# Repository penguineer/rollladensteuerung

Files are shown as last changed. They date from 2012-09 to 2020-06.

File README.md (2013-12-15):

Rolladensteuerung
=================

Content

controller:       Relais-Controller Rollläden
manuellsteuerung: Schalter für Manuellbetrieb Rollläden
raspberry:        Software für den Kontroll-Raspy
relaiskarte:      Relais Rollläden
switchboard:      Altes Schalterboard
tuer-controller:  I2C-Bridge zur Tür-Steuerung
tuer-steuerung:   Kontrolle Motor und Türstatus-Schalter
wd-switch:        Watchdog-Switch für Reset per Raspy

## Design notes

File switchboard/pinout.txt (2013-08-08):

DSUB:
pin#	funcion (0/1)
1	vcc
2	out 1 (up/down)
3	out 2 (up/down)
4	out 3 (up/down)
5	out 4 (up/down)
6	out 1 (off/on)
7	out 2 (off/on)
8	out 3 (off/on)
9	out 4 (off/on)

Molex:
1	5V
2	GND
3	GND
4	12V - not used

orange headers:
2pin	230V in
3pin	GND-UP-DOWN

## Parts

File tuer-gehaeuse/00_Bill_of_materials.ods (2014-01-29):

Pos.Nr. | Titel | Material | Menge | Bemerkung | Bezugsquellen | PDF | DXF | STL
1 | Schließblech | Stahl | 1 | Bereits vorhanden | -o-
2 | Sechskantschraube ISO 4017 - M6x30 | Stahl | 2 |  | Ebay/Baumarkt
3 | Scheibe ANSI B18.22M regulär 6 mm | Stahl | 13 |  | Ebay/Baumarkt
4 | Sechskantmutter ISO 4032 - M6 | Stahl | 14 |  | Ebay/Baumarkt
5 | Tür-Motor-Koppler | Holz, Kiefer | 1 |  | Baumarkt | File | File | File
6 | Sechskantschraube ISO 4017 - M6x80 | Stahl | 4 |  | Ebay/Baumarkt
7 | Getriebemotor | Materialverbund | 1 |  | http://www.pollin.de/shop/dt/MjI1OTg2OTk-/Motoren/DC_Getriebemotoren/Gleichstrom_Getriebemotor_GMPD_404980_1_12_V_.html
8 | Drehring | ABS Plastik, hochfest | 1 | Bestandteil des Motors | -o-
9 | Schlüsselhalter | ABS Plastik, hochfest | 1 | Kopf ist an Schlüssel anzupassen | Internet | File |  | File
10 | Ritzel | Acryl | 1 |  | Ebay | File | File
11 | Zahnrad | Acryl | 1 |  | Ebay | File | File
12 | Kugellager 608Z Di=8mm Da=22m | Stahl | 2 |  | Ebay
13 | M8x80 Gewindestange | Stahl | 1 | Als Welle für Zahnrad | Ebay/Baumarkt
14 | M8 Mutter | Stahl | 5 |  | Ebay/Baumarkt
15 | Washer DIN 6902 - A M8 - 200 HV | Stahl | 2 |  | Ebay/Baumarkt
16 | Gehäuseverbinder | Holz, Kiefer | 1 |  | Baumarkt | File |  | File
17 | Gehäusehälfte 2 | Holz, Kiefer | 1 |  | Baumarkt | File | File | File
18 | Spacer: Motor-Ritzel | PLA | 1 |  | Internet | File | File | File
19 | Exzenter | PLA | 2 |  | Internet | File |  | File
20 | M3x12-Senkkopfschraube | Stahl | 2 | Zur Montage der Exzenter | Ebay/Baumarkt
21 | Endschalter | Materialverbund | 2 |  | http://reprapuniverse.com/catalog/product_info.php?cPath=28&products_id=41
22 | Drahtstift | Stahl | 4 | Nicht eingezeichnet, zur Montage der Endschalter | Ebay/Baumarkt
23 | Spacer: Enschalter-Hälfte 2 | Holz, Kiefer | 1 |  | Baumarkt | File | File | File
24 | Fassschutz_hinten | Acryl | 1 |  | Ebay | File | File
25 | Fassschutz_vorn | Acryl | 1 |  | Ebay | File | File
26 | Fassschutz_oben | Acryl | 1 |  | Ebay | File | File
27 | Fassschutz_rechts | Acryl | 1 |  | Ebay | File | File
28 | Fassschutz_links | Acryl | 1 |  | Ebay | File | File
29 | Fassschutz_unten | Acryl | 1 |  | Ebay | File | File
30 | 3mm LED rot | Materialverbund | 3 | Nicht eingezeichnet, werden in Fassschutz_hinten geklebt | http://www.ebay.de/itm/370921378597?ssPageName=STRK:MEWNX:IT&_trksid=p3984.m1439.l2649
31 | 3mm LED grün | Materialverbund | 3 | Nicht eingezeichnet, werden in Fassschutz_vorn geklebt | http://www.ebay.de/itm/370921405223?ssPageName=STRK:MEWNX:IT&_trksid=p3984.m1439.l2649

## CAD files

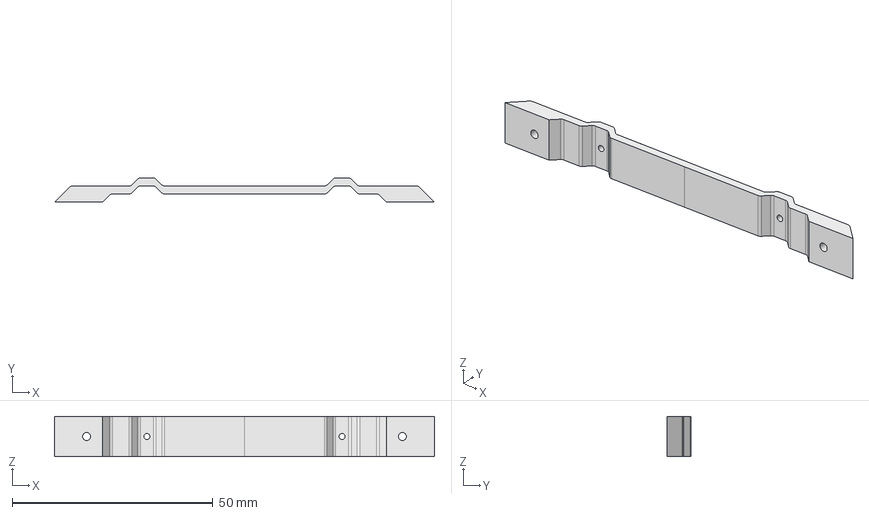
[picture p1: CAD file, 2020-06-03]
pi-hat/halterung.FCStd
94.6 x 6.00 x 10.0 mm

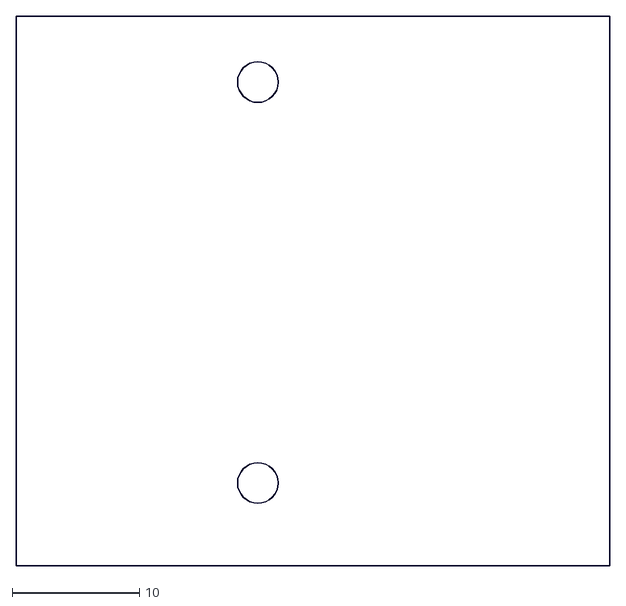
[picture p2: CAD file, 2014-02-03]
tuer-controller/tuer-controller-dim.dxf
46.7 x 43.2

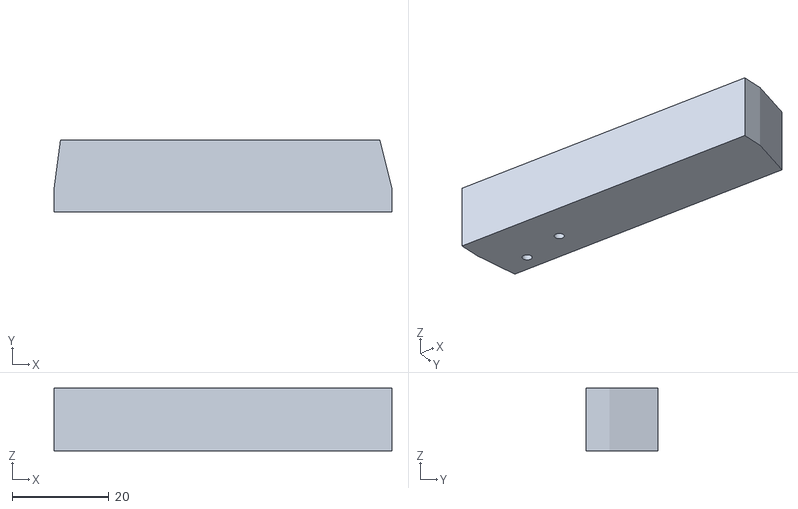
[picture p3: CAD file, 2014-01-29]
tuer-gehaeuse/Endschalter-Haelfte2.stl
70.0 x 15.0 x 13.0

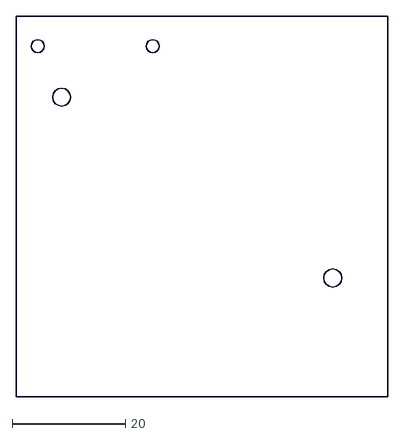
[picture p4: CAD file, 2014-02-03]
tuer-steuerung/tuer-steuerung-dim.dxf
65.7 x 67.3

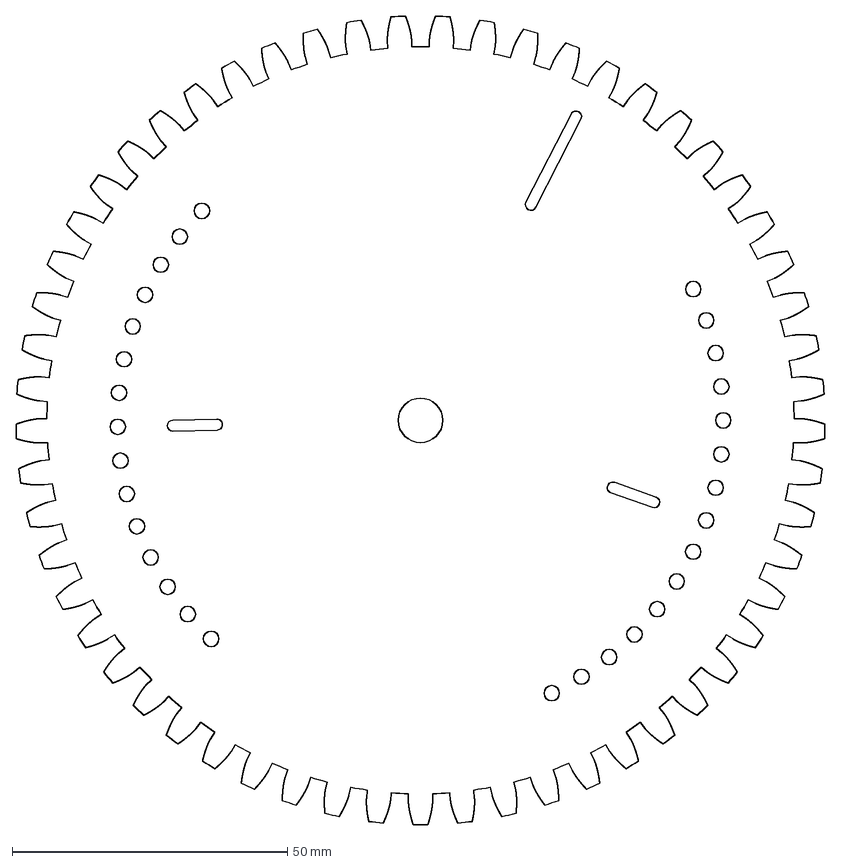
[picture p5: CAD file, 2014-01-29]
tuer-gehaeuse/Zahnrad.dxf
147.0 x 146.9 mm

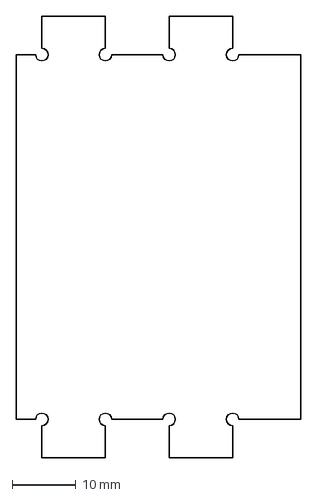
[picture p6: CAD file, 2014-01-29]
tuer-gehaeuse/Fassschutz_unten.dxf
44.7 x 69.4 mm

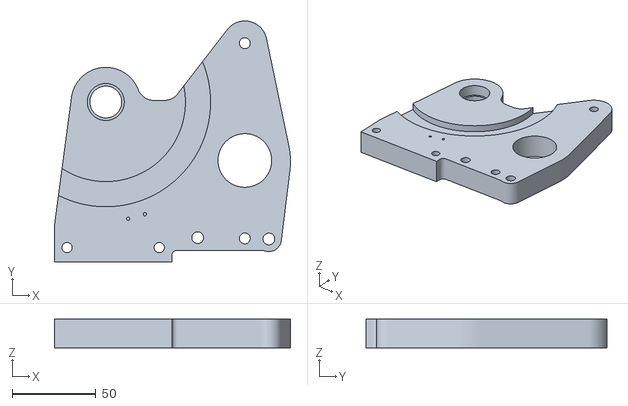
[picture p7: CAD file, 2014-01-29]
tuer-gehaeuse/Tuer_Motor_Koppler.stl
140.8 x 143.8 x 17.2

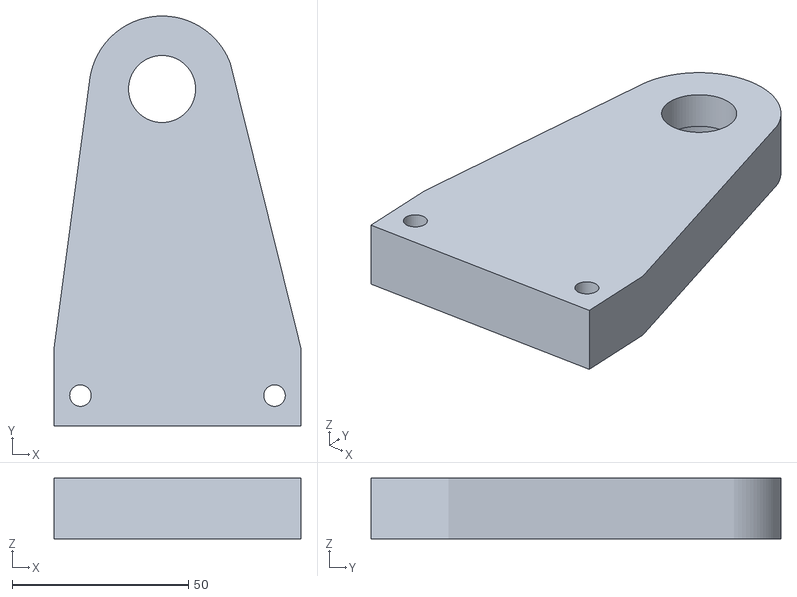
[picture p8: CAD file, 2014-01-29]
tuer-gehaeuse/Gehaeuesehaelfte_2.stl
70.0 x 116.2 x 17.2

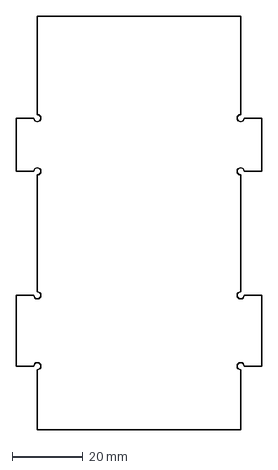
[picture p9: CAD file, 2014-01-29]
tuer-gehaeuse/Fassschutz_rechts.dxf
69.4 x 116.8 mm

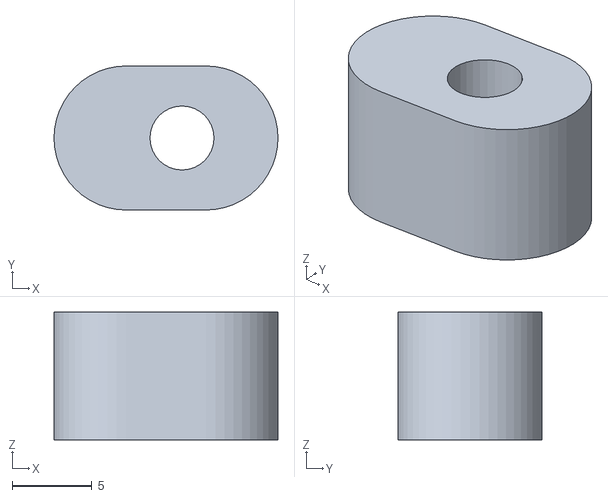
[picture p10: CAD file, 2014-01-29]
tuer-gehaeuse/Exzenter.stl
14.0 x 9.00 x 8.00

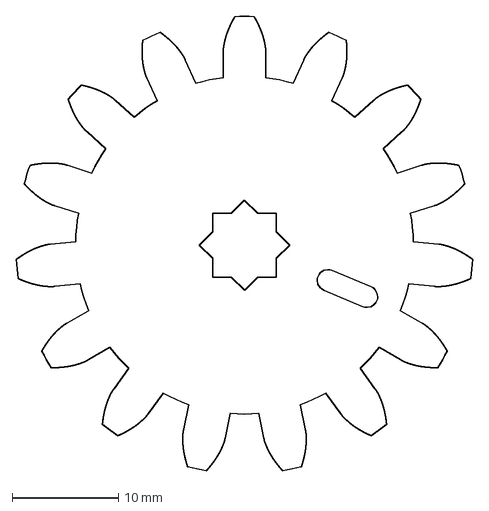
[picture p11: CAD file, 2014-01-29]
tuer-gehaeuse/Ritzel.dxf
42.9 x 42.7 mm

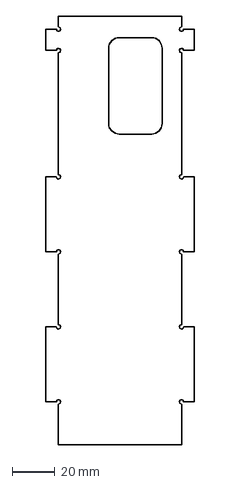
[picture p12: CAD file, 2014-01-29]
tuer-gehaeuse/Fassschutz_oben.dxf
69.4 x 200.0 mm

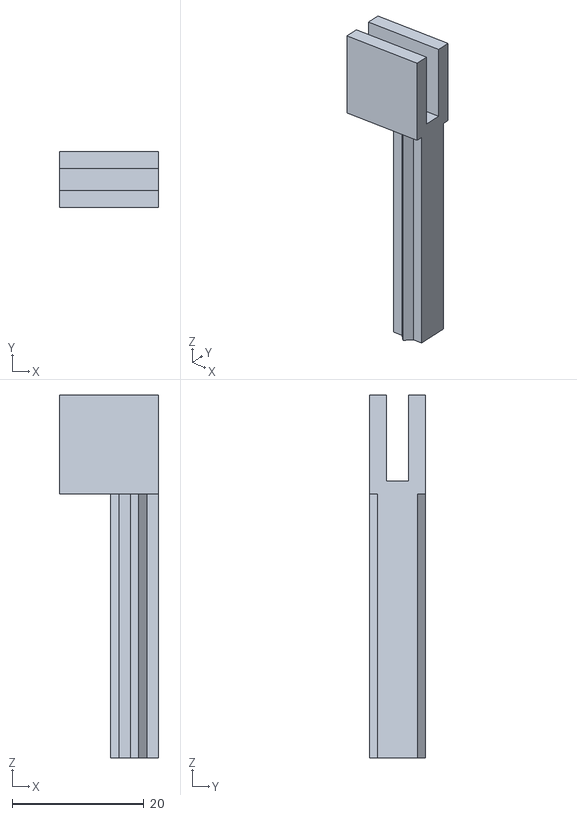
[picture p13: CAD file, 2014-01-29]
tuer-gehaeuse/Schluesselhalter.stl
15.0 x 8.49 x 55.0

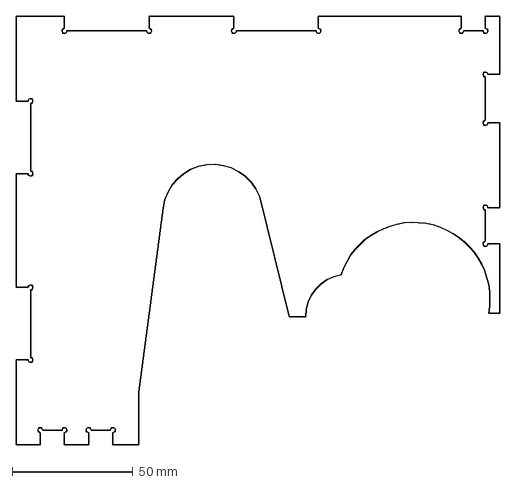
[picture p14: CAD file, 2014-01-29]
tuer-gehaeuse/Fassschutz_vorn.dxf
200.0 x 177.0 mm

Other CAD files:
tuer-schalter/skizze.fcstd
tuer-gehaeuse/01_Hardware_00.stp
tuer-gehaeuse/Gehaeueseverbinder.stl
tuer-gehaeuse/Fassschutz_links.dxf
tuer-gehaeuse/Endschalter-Haelfte2.dxf
tuer-gehaeuse/Fassschutz_hinten.dxf
tuer-gehaeuse/Gehaeuesehaelfte_2.dxf
tuer-gehaeuse/Spacer_Motor_Ritzel.dxf
tuer-gehaeuse/Spacer_Motor_Ritzel.stl
tuer-gehaeuse/Tuer_Motor_Koppler.dxf

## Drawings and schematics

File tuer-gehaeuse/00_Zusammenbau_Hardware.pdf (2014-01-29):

B

A

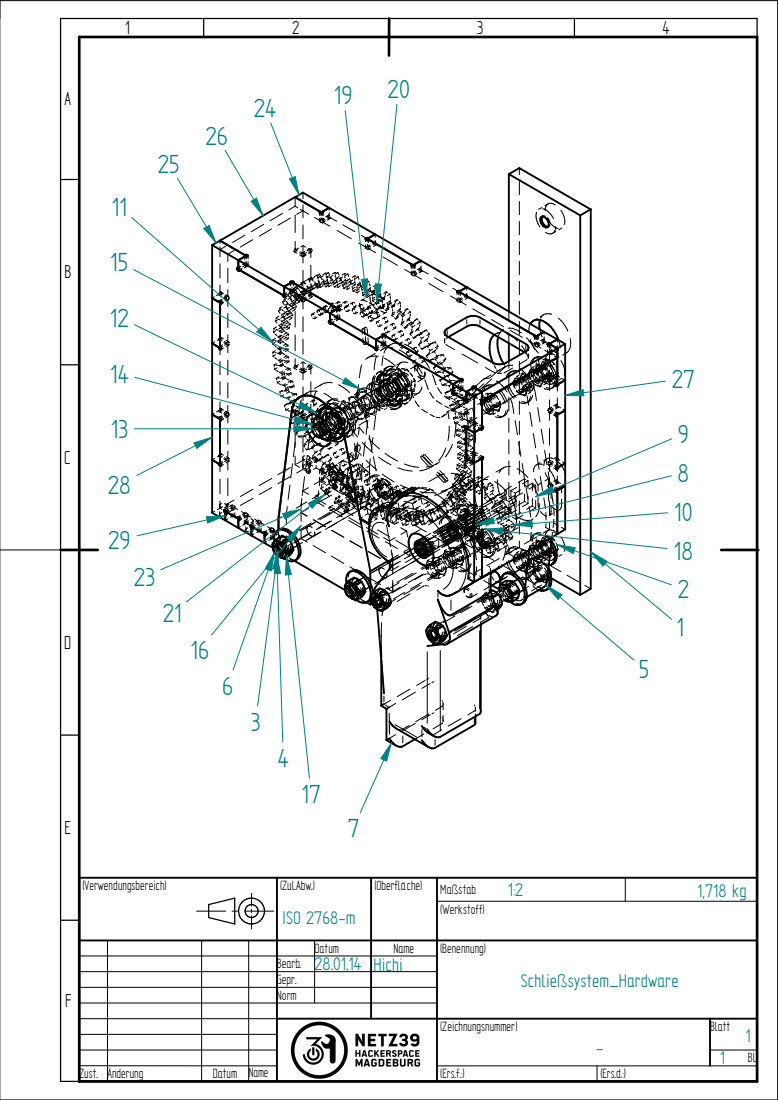
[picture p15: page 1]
Zust.; Änderung; Datum; Name; Maßstab; Blatt; (Zeichnungsnummer); 1,718 kg ⁽Zul.Abw.); (Oberfläche); (Werkstoff); (Ers.f.:); (Ers.d.:); (Verwendungsbereich); ISO 2768-m

Datum | Name | (Benennung) Schließsystem_Hardware
Bearb. | 28.01.14 | Hichi
Gepr.
Norm

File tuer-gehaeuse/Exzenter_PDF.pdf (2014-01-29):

B

A

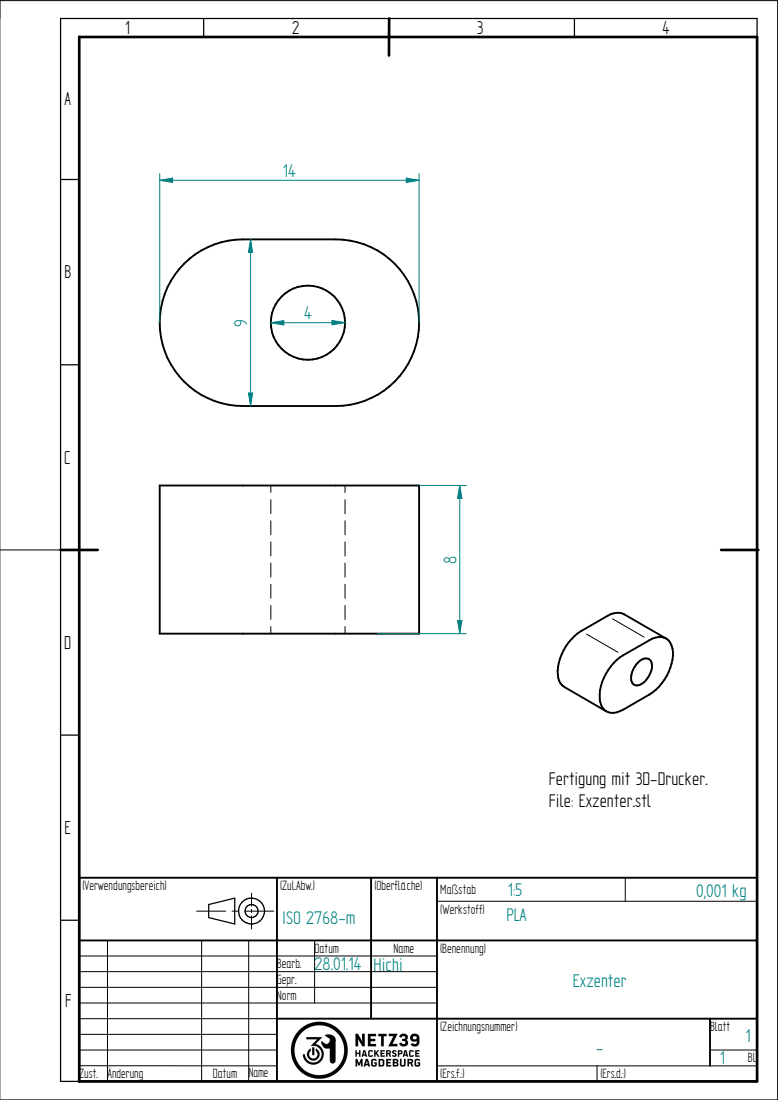
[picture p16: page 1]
Zust.; Änderung; Datum; Name; Maßstab; Blatt; (Zeichnungsnummer); 0,001 kg ⁽Zul.Abw.); (Oberfläche); (Werkstoff); (Ers.f.:); (Ers.d.:); (Verwendungsbereich); ISO 2768-m; PLA

Fertigung mit 3D-Drucker.
File: Exzenter.stl

Datum | Name | (Benennung) Exzenter
Bearb. | 28.01.14 | Hichi
Gepr.
Norm

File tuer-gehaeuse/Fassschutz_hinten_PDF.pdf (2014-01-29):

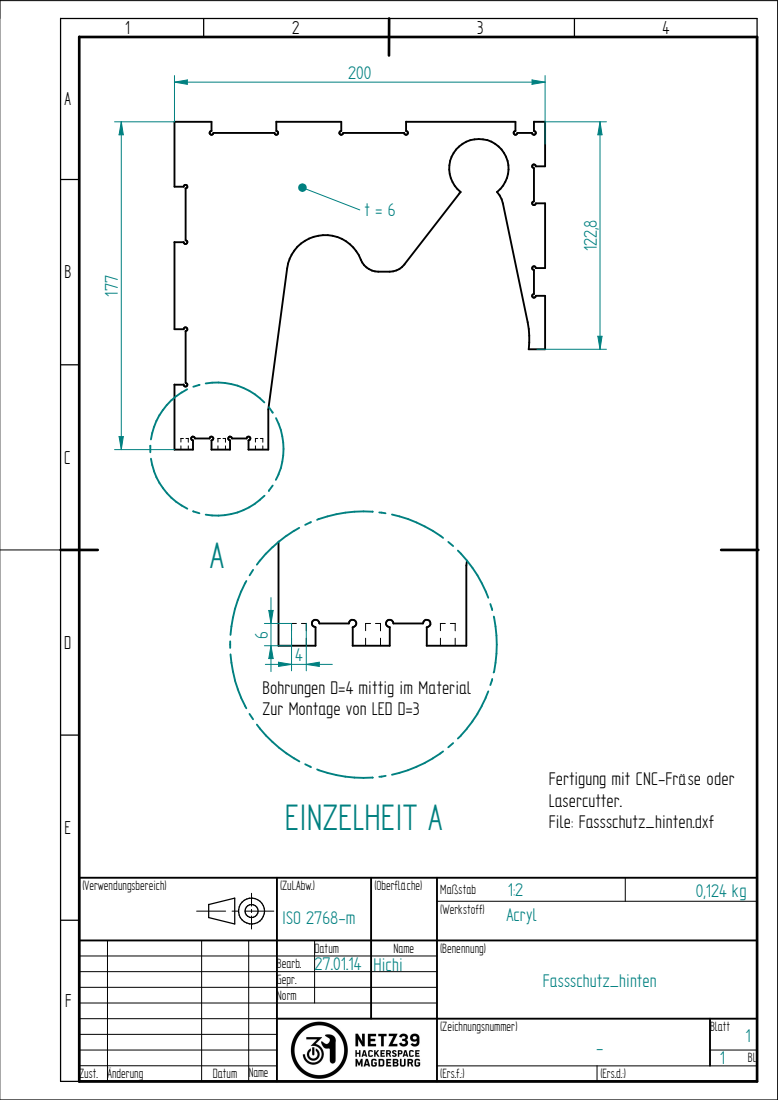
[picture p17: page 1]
Zust.; Änderung; Datum; Name; Maßstab; Blatt; (Zeichnungsnummer); 0,124 kg ⁽Zul.Abw.); (Oberfläche); (Werkstoff); (Ers.f.:); (Ers.d.:); (Verwendungsbereich); Acryl ISO 2768-m; EINZELHEIT A

Bohrungen D=4 mittig im Material
Zur Montage von LED D=3

Fertigung mit CNC-Fräse oder
Lasercutter.
File: Fassschutz_hinten.dxf

Datum | Name | (Benennung) Fassschutz_hinten
Bearb. | 27.01.14 | Hichi
Gepr.
Norm

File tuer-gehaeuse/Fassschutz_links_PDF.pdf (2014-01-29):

B

A

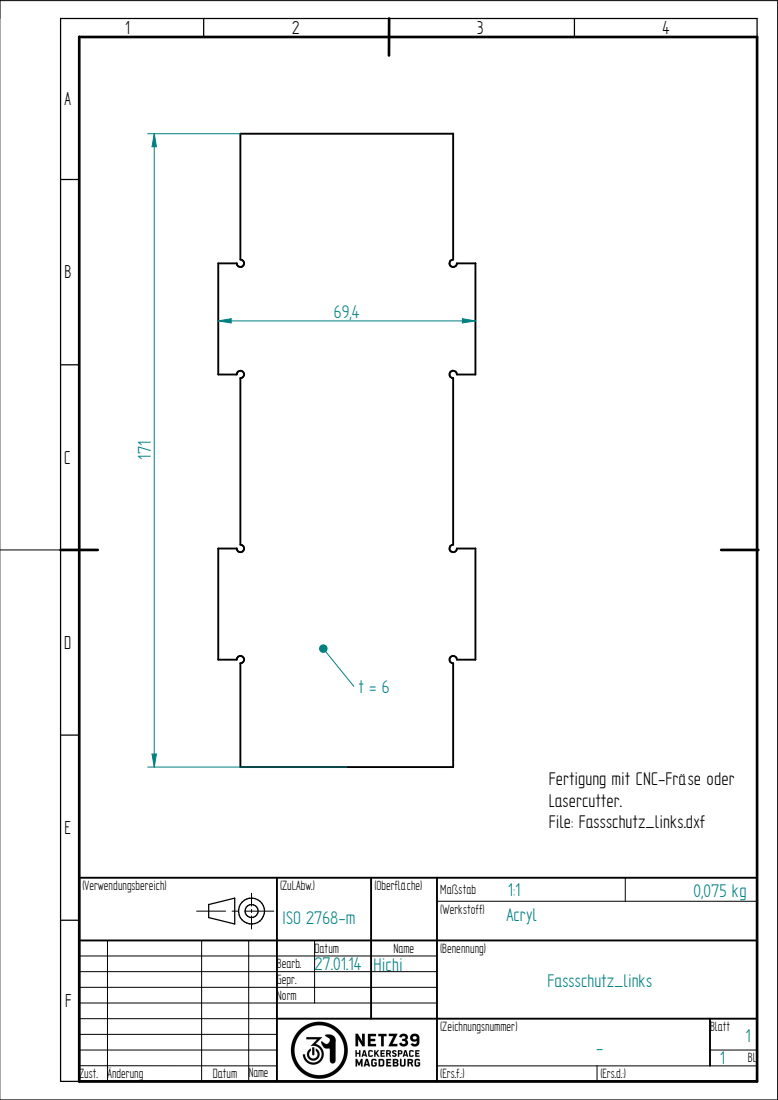
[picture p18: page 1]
Zust.; Änderung; Datum; Name; Maßstab; Blatt; (Zeichnungsnummer); 0,075 kg ⁽Zul.Abw.); (Oberfläche); (Werkstoff); (Ers.f.:); (Ers.d.:); (Verwendungsbereich); Acryl ISO 2768-m

Fertigung mit CNC-Fräse oder
Lasercutter.
File: Fassschutz_links.dxf

Datum | Name | (Benennung) Fassschutz_links
Bearb. | 27.01.14 | Hichi
Gepr.
Norm

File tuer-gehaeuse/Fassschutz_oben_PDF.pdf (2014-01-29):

B

A

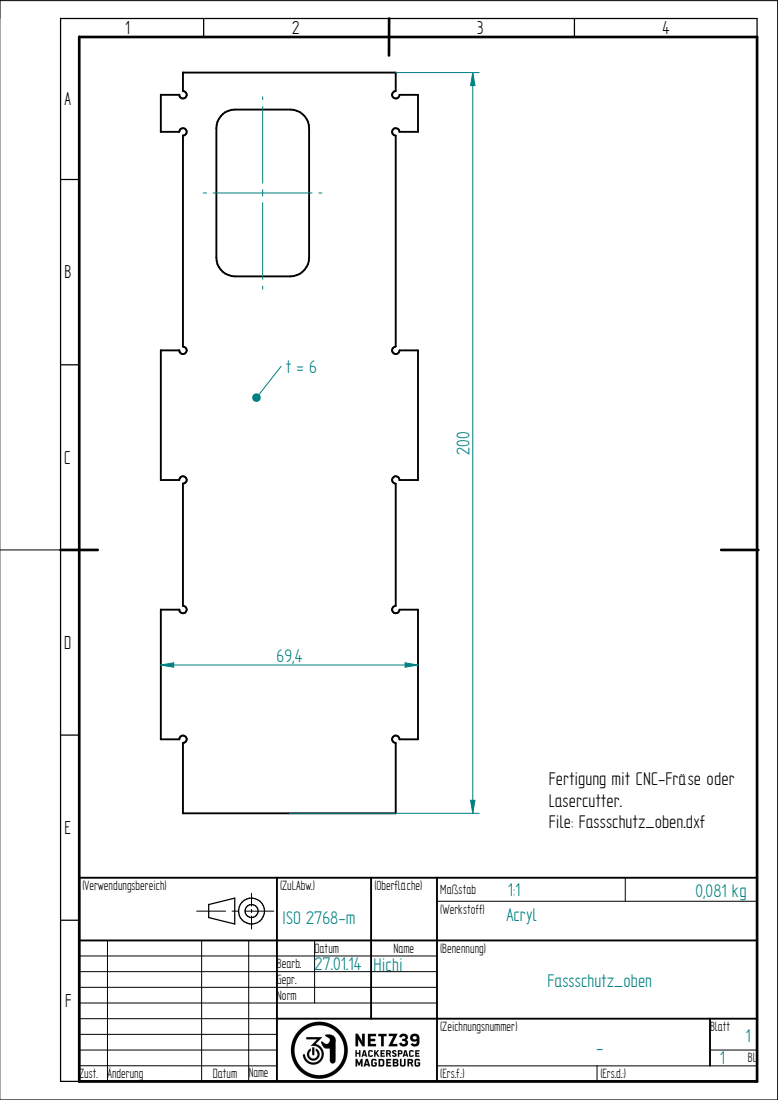
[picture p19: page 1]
Zust.; Änderung; Datum; Name; Maßstab; Blatt; (Zeichnungsnummer); 0,081 kg ⁽Zul.Abw.); (Oberfläche); (Werkstoff); (Ers.f.:); (Ers.d.:); (Verwendungsbereich); Acryl ISO 2768-m

Fertigung mit CNC-Fräse oder
Lasercutter.
File: Fassschutz_oben.dxf

Datum | Name | (Benennung) Fassschutz_oben
Bearb. | 27.01.14 | Hichi
Gepr.
Norm

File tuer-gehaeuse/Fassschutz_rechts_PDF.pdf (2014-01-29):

B

A

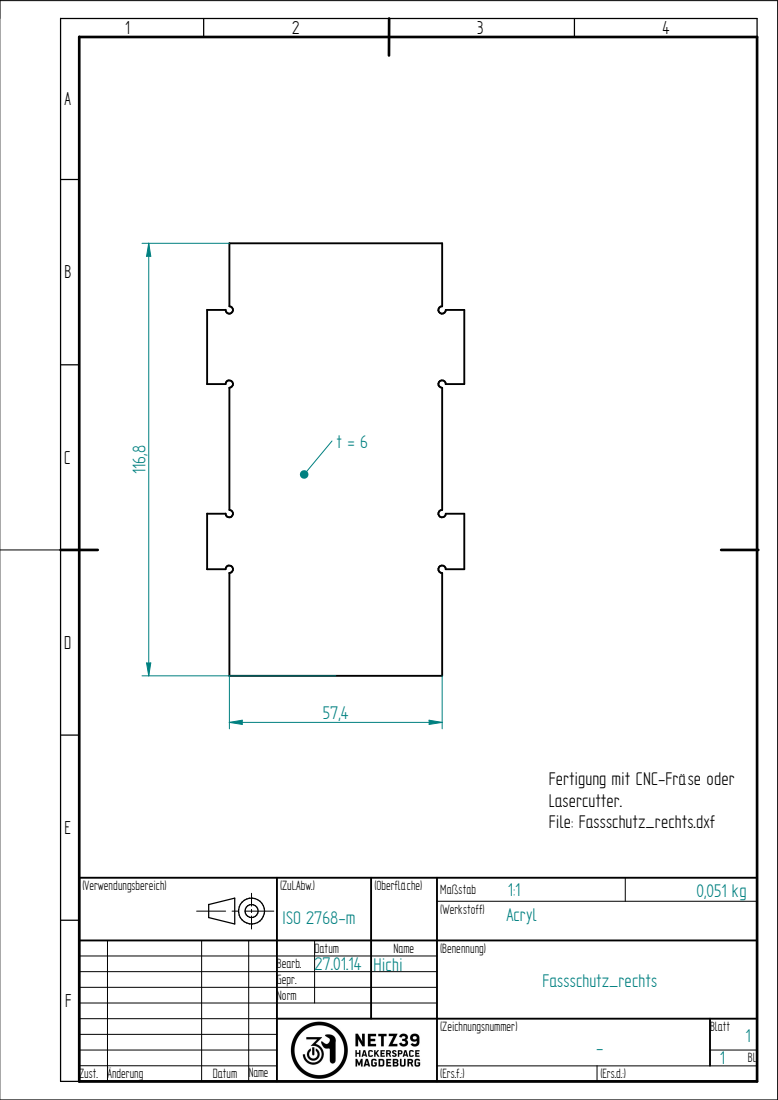
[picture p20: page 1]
Zust.; Änderung; Datum; Name; Maßstab; Blatt; (Zeichnungsnummer); 0,051 kg ⁽Zul.Abw.); (Oberfläche); (Werkstoff); (Ers.f.:); (Ers.d.:); (Verwendungsbereich); Acryl ISO 2768-m

Fertigung mit CNC-Fräse oder
Lasercutter.
File: Fassschutz_rechts.dxf

Datum | Name | (Benennung) Fassschutz_rechts
Bearb. | 27.01.14 | Hichi
Gepr.
Norm

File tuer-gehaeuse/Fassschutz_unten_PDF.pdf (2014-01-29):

B

A

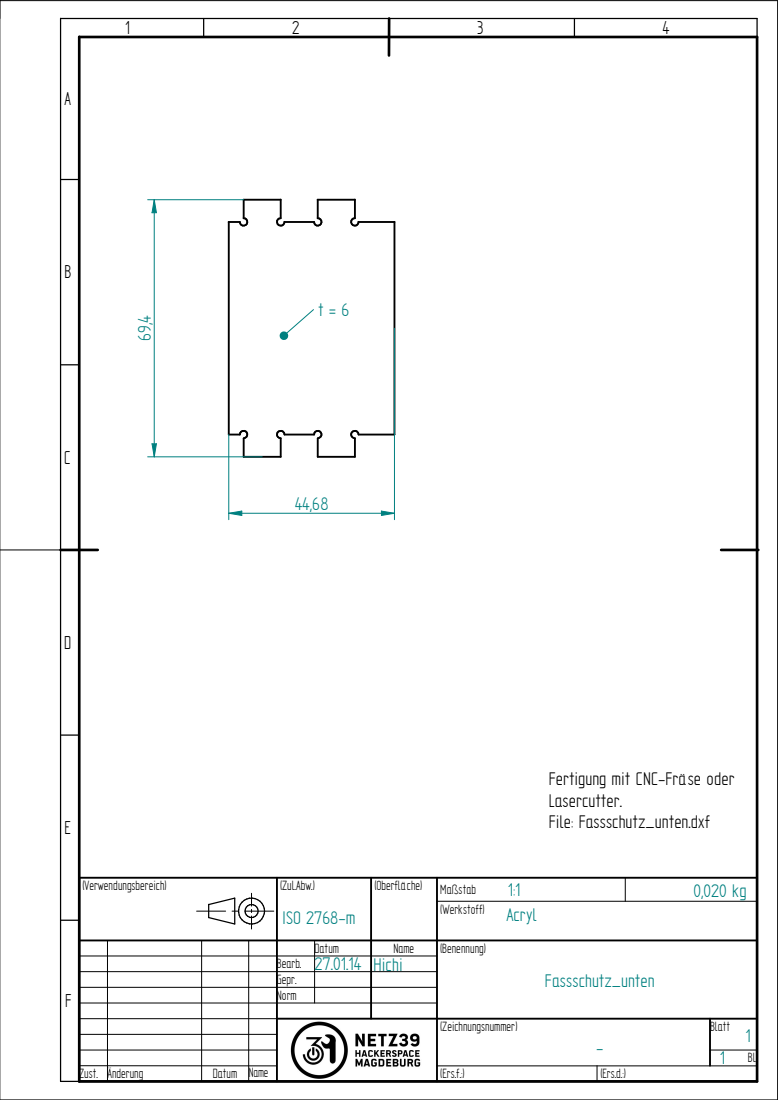
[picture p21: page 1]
Zust.; Änderung; Datum; Name; Maßstab; Blatt; (Zeichnungsnummer); 0,020 kg ⁽Zul.Abw.); (Oberfläche); (Werkstoff); (Ers.f.:); (Ers.d.:); (Verwendungsbereich); Acryl ISO 2768-m

Fertigung mit CNC-Fräse oder
Lasercutter.
File: Fassschutz_unten.dxf

Datum | Name | (Benennung) Fassschutz_unten
Bearb. | 27.01.14 | Hichi
Gepr.
Norm

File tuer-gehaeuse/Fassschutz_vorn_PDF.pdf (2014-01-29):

B

A

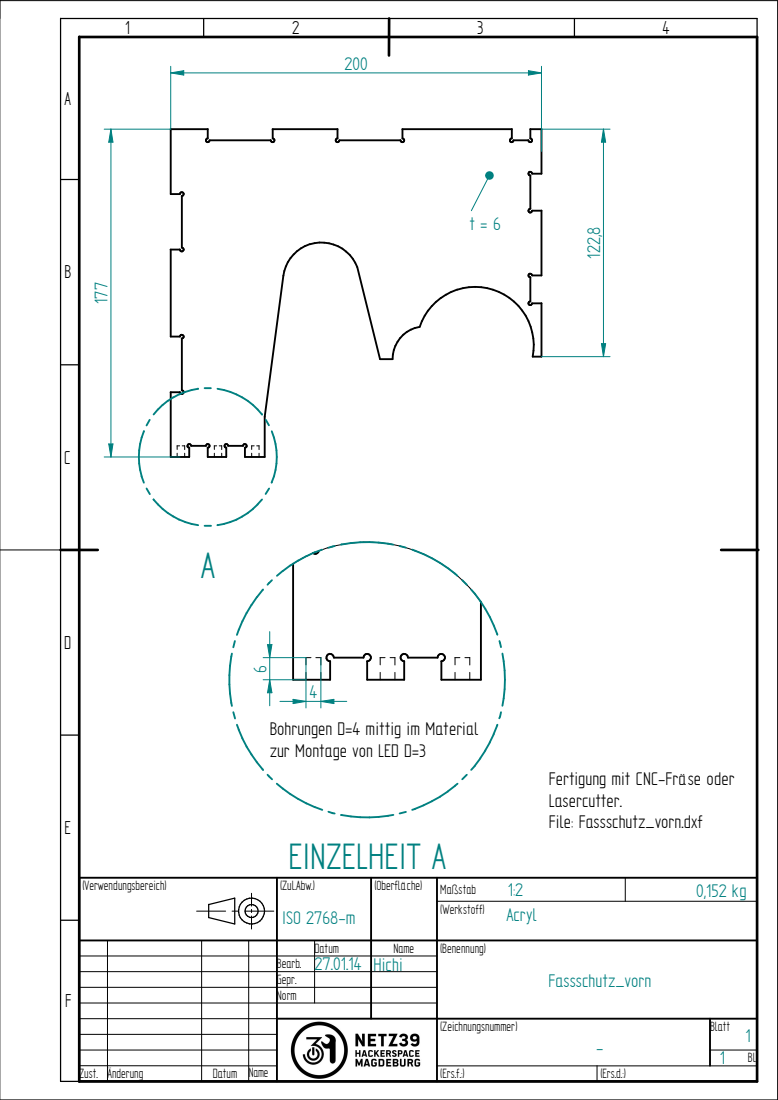
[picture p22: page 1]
Zust.; Änderung; Datum; Name; Maßstab; Blatt; (Zeichnungsnummer); 0,152 kg ⁽Zul.Abw.); (Oberfläche); (Werkstoff); (Ers.f.:); (Ers.d.:); (Verwendungsbereich); Acryl ISO 2768-m; EINZELHEIT A

Bohrungen D=4 mittig im Material
zur Montage von LED D=3

Fertigung mit CNC-Fräse oder
Lasercutter.
File: Fassschutz_vorn.dxf

Datum | Name | (Benennung) Fassschutz_vorn
Bearb. | 27.01.14 | Hichi
Gepr.
Norm

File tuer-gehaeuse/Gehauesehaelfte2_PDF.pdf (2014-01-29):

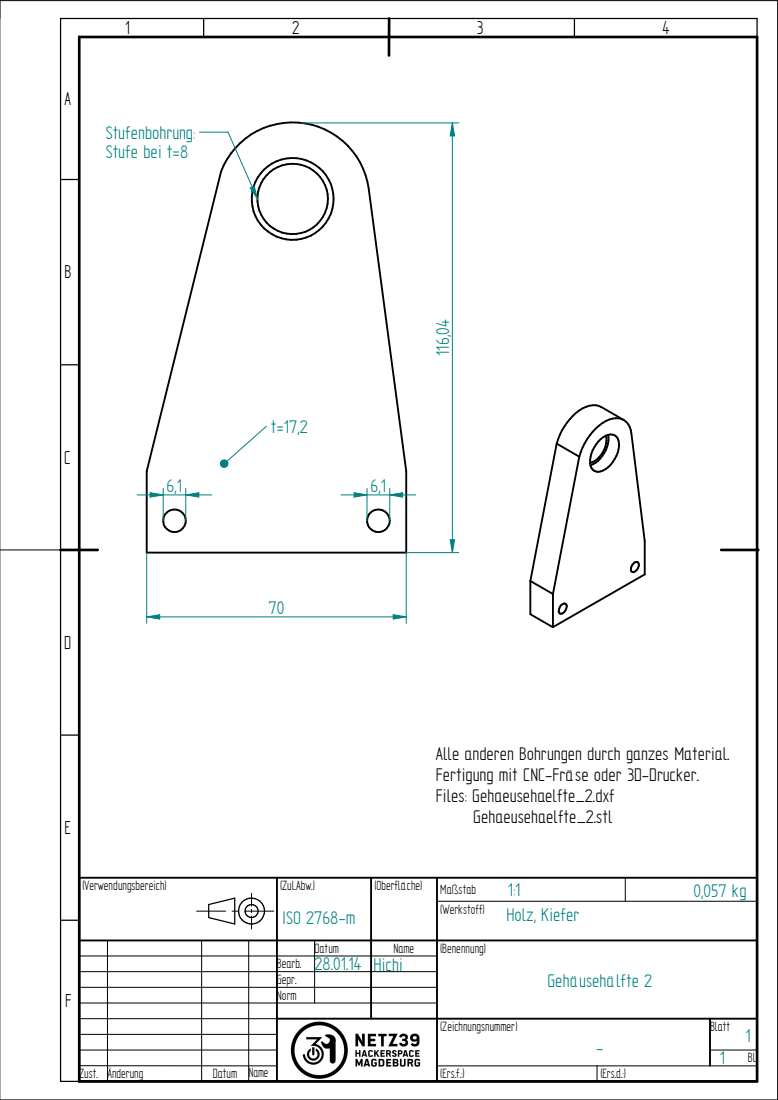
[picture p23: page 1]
Zust.; Änderung; Datum; Name; Maßstab; Blatt; (Zeichnungsnummer); 0,057 kg ⁽Zul.Abw.); (Oberfläche); (Werkstoff); (Ers.f.:); (Ers.d.:); (Verwendungsbereich); ISO 2768-m; Holz, Kiefer ¹¹⁶,04; Stufenbohrung: Stufe bei t=8

Alle anderen Bohrungen durch ganzes Material.
Fertigung mit CNC-Fräse oder 3D-Drucker.
Files: Gehaeusehaelfte_2.dxf
Gehaeusehaelfte_2.stl

Datum | Name | (Benennung) Gehäusehälfte 2
Bearb. | 28.01.14 | Hichi
Gepr.
Norm

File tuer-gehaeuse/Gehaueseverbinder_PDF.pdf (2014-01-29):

B

A

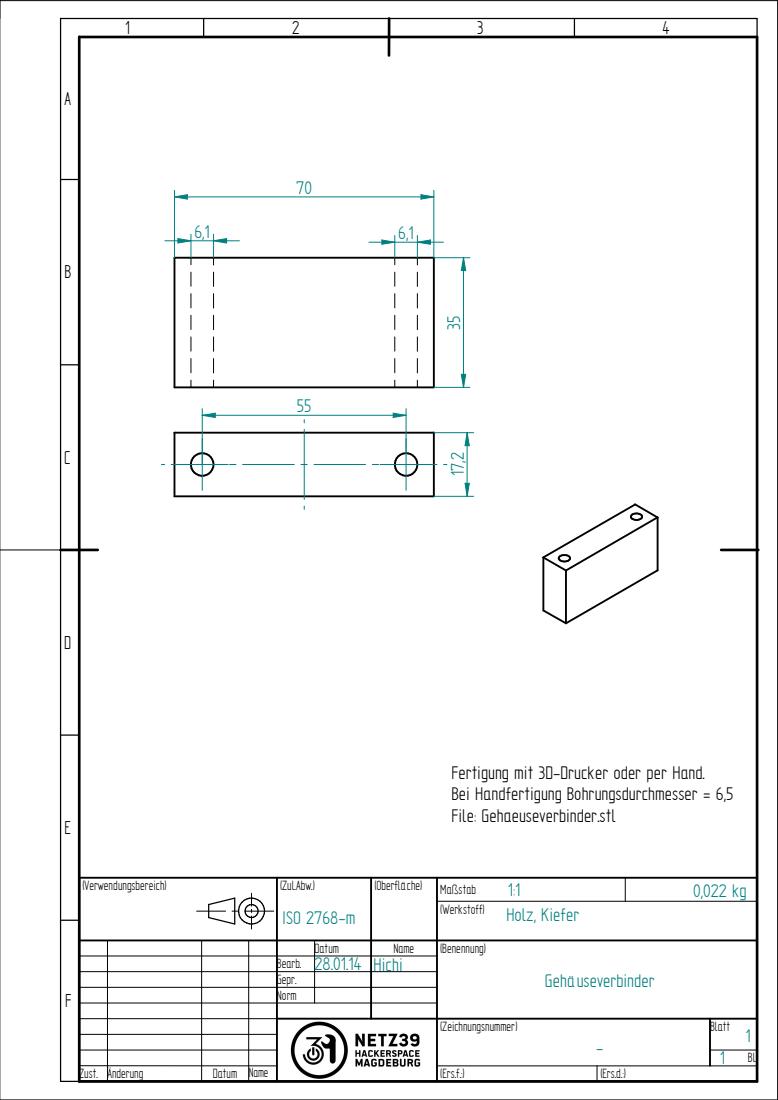
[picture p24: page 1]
Zust.; Änderung; Datum; Name; Maßstab; Blatt; (Zeichnungsnummer); 0,022 kg ⁽Zul.Abw.); (Oberfläche); (Werkstoff); (Ers.f.:); (Ers.d.:); (Verwendungsbereich); ISO 2768-m; Holz, Kiefer

Fertigung mit 3D-Drucker oder per Hand.
Bei Handfertigung Bohrungsdurchmesser = 6,5
File: Gehaeuseverbinder.stl

Datum | Name | (Benennung) Gehäuseverbinder
Bearb. | 28.01.14 | Hichi
Gepr.
Norm

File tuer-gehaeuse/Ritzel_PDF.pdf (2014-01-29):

B

A

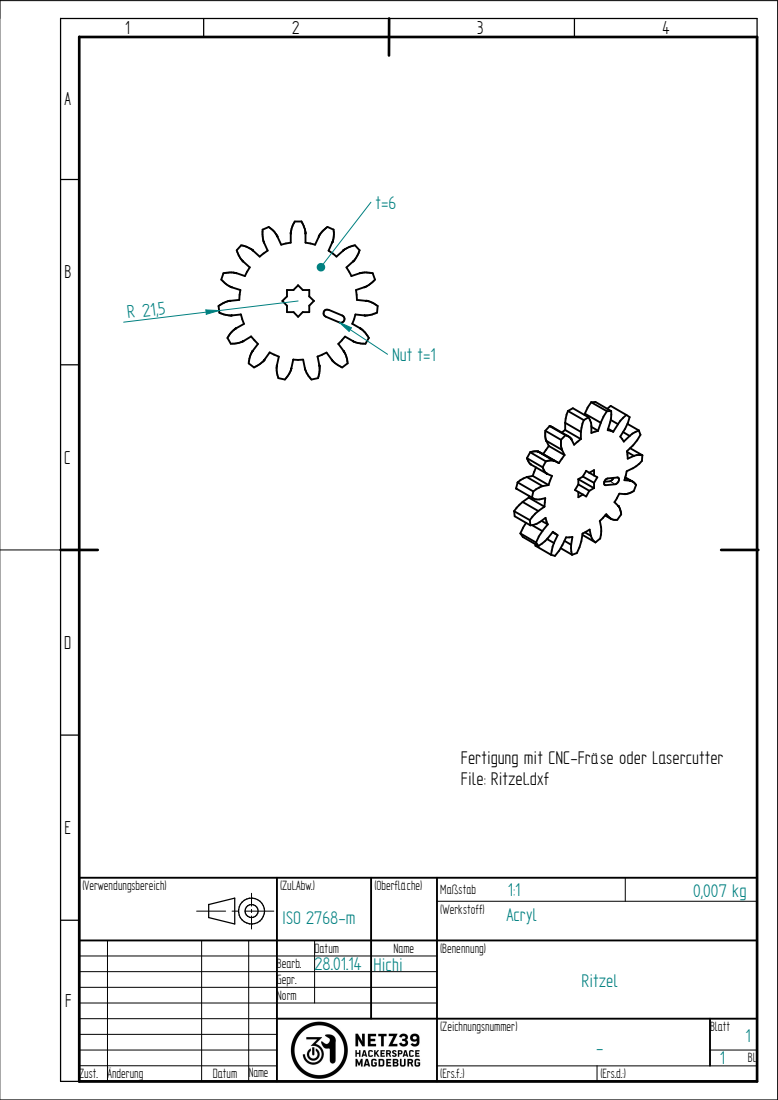
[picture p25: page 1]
Zust.; Änderung; Datum; Name; Maßstab; Blatt; (Zeichnungsnummer); 0,007 kg ⁽Zul.Abw.); (Oberfläche); (Werkstoff); (Ers.f.:); (Ers.d.:); (Verwendungsbereich); Acryl ISO 2768-m; Nut t=1

Fertigung mit CNC-Fräse oder Lasercutter
File: Ritzel.dxf

Datum | Name | (Benennung) Ritzel
Bearb. | 28.01.14 | Hichi
Gepr.
Norm

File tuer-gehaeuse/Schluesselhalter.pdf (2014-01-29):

B

A

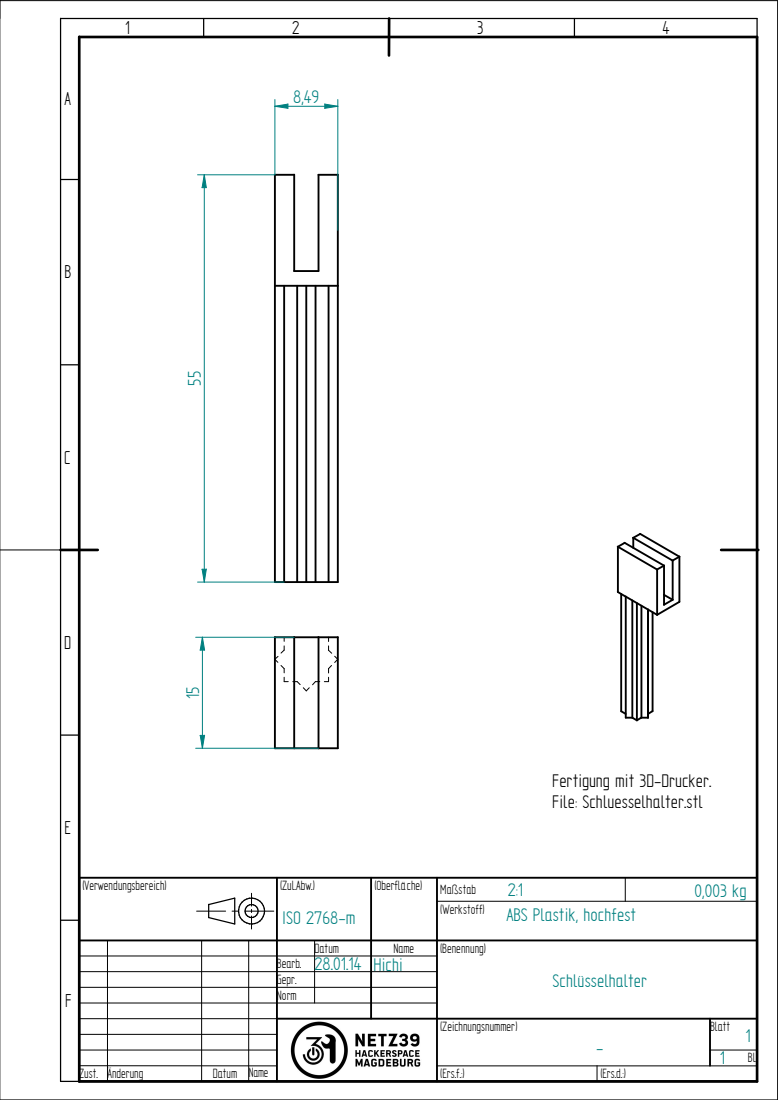
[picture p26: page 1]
Zust.; Änderung; Datum; Name; Maßstab; Blatt; (Zeichnungsnummer); 0,003 kg ⁽Zul.Abw.); (Oberfläche); (Werkstoff); (Ers.f.:); (Ers.d.:); (Verwendungsbereich); ISO 2768-m; ABS Plastik, hochfest

Fertigung mit 3D-Drucker.
File: Schluesselhalter.stl

Datum | Name | (Benennung) Schlüsselhalter
Bearb. | 28.01.14 | Hichi
Gepr.
Norm

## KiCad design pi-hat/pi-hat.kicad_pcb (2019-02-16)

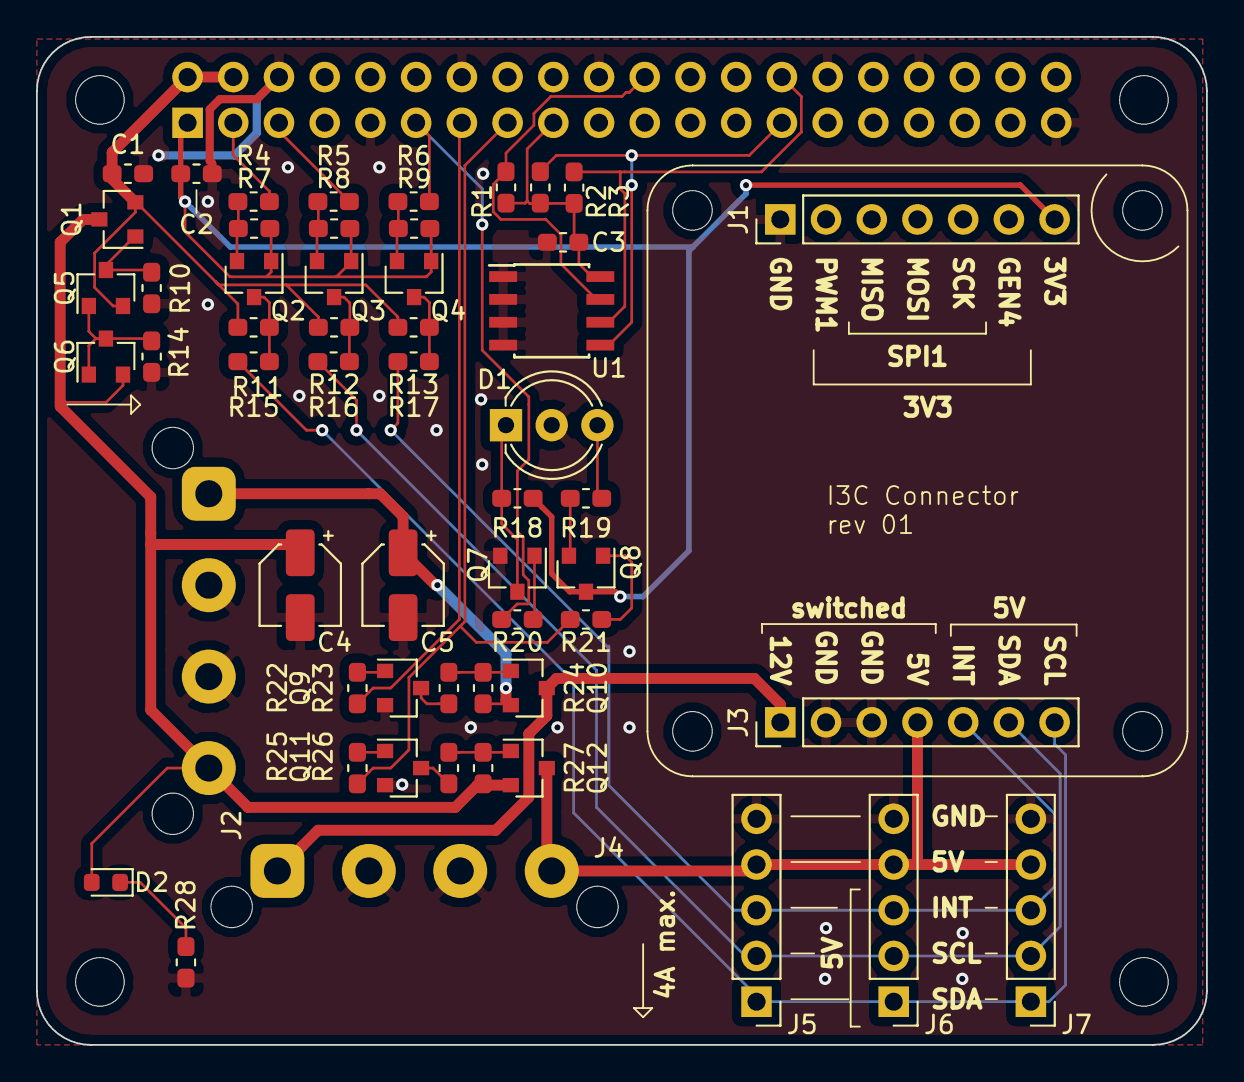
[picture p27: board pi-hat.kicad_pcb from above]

Board: 2 copper layers, 65.0 x 56.0 mm, 64 parts (1 on the bottom side), 39 nets.

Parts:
C1, C2, C3: 100n; C_0603_1608Metric_Pad1.05x0.95mm_HandSolder
C4, C5: 47u; CP_Elec_4x4.5
D1: LED5 RG-3; LED_D5.0mm-3
D2: LED; LED_0603_1608Metric
J1, J3: Conn_01x07_Male; PinHeader_1x07_P2.54mm_Vertical
J2, J4: Conn_01x04_Male; MOLEX-HDD-PWR-horizontal
J5, J6, J7: Conn_01x05_Male; PinHeader_1x05_P2.54mm_Vertical
MK1, MK2, MK7, MK8: M2.5; MountingHole_2.7mm_M2.5
MK3, MK4, MK5, MK6: 2.0; MountingHole_2.2mm_M2_DIN965
P1: Conn_02x20_Odd_Even; PinSocket_2x20_P2.54mm_Vertical
Q1, Q10, Q12: AO 3415A; SOT-23
Q2, Q3, Q4: BSS138; SOT-23
Q5, Q6: BC 807-25; SOT-23
Q7, Q8, Q9, Q11: BC 818-25; SOT-23
R1, R7, R8, R9, R11, R12, R13, R14, R24, R27: 10K; C_0603_1608Metric_Pad1.05x0.95mm_HandSolder
R2, R3: 3K9; C_0603_1608Metric_Pad1.05x0.95mm_HandSolder
R4, R5, R6, R15, R16, R17, R23, R26: 10R; C_0603_1608Metric_Pad1.05x0.95mm_HandSolder
R10: 47K; C_0603_1608Metric_Pad1.05x0.95mm_HandSolder
R18, R19, R28: 150R; C_0603_1608Metric_Pad1.05x0.95mm_HandSolder
R20, R21, R22, R25: 330R; C_0603_1608Metric_Pad1.05x0.95mm_HandSolder
U1: M24C02-WMN; SOIC-8_3.9x4.9mm_P1.27mm

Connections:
+3.3VA: C3.1, P1.17, R1.1, R2.1, R3.1, U1.8
+3V3: C2.1, J1.7, P1.1, Q2.1, Q3.1, Q4.1, Q8.3, R7.1, R8.1, R9.1, R18.1
+5V: C1.1, P1.2, P1.4, Q1.2, Q5.2, R11.1, R12.1, R13.1
+5VA: J3.4, J4.4, J5.4, J6.4, J7.4, Q12.3
+5VP: C4.1, D2.2, J2.4, Q1.3, Q6.2, Q12.2, R27.1
+12V: C5.1, J2.1, Q10.2, R24.1
+12VA: J3.1, J4.1, Q10.3
ACTIVATE_5V: P1.15, R21.1, R25.2
ACTIVATE_12V: P1.13, R22.2
GND: C1.2, C2.2, C3.2, C4.2, C5.2, D1.2, J1.1, J2.2, J2.3, J3.2, J3.3, J4.2, J4.3, J5.5, J6.5, J7.5, P1.6, P1.9, P1.14, P1.20, P1.25, P1.30, P1.34, P1.39, Q7.2, Q9.2, Q11.2, R10.2, R14.2, R28.2, U1.1, U1.2, U1.3, U1.4
ID_SC: P1.28, R3.2, U1.6
ID_SD: P1.27, R2.2, U1.5
ID_WP: P1.22, R1.2, U1.7
INT: P1.11, R6.2, R20.2
INT_5V: J3.5, J5.3, J6.3, J7.3, R17.1
unnamed: D1.1, Q7.3, R18.2
unnamed: D1.3, R19.2
unnamed: D2.1, R28.1
unnamed: Q2.2, R4.1, R7.2
unnamed: Q2.3, R11.2, R15.2
unnamed: Q3.2, R5.1, R8.2
unnamed: Q3.3, R12.2, R16.2
unnamed: Q4.2, R6.1, R9.2
unnamed: Q4.3, R13.2, R17.2
unnamed: Q5.1, Q6.1, Q6.3, R14.1
unnamed: Q1.1, Q5.3, R10.1
unnamed: Q7.1, R20.1
unnamed: Q8.1, R21.2
unnamed: Q8.2, R19.1
unnamed: Q9.1, R22.1
unnamed: Q9.3, R23.2
unnamed: Q10.1, R23.1, R24.2
unnamed: Q11.1, R25.1
unnamed: Q11.3, R26.2
unnamed: Q12.1, R26.1, R27.2
SCL: P1.5, R5.2
SCL_5V: J3.6, J5.2, J6.2, J7.2, R16.1
SDA: P1.3, R4.2
SDA_5V: J3.7, J5.1, J6.1, J7.1, R15.1

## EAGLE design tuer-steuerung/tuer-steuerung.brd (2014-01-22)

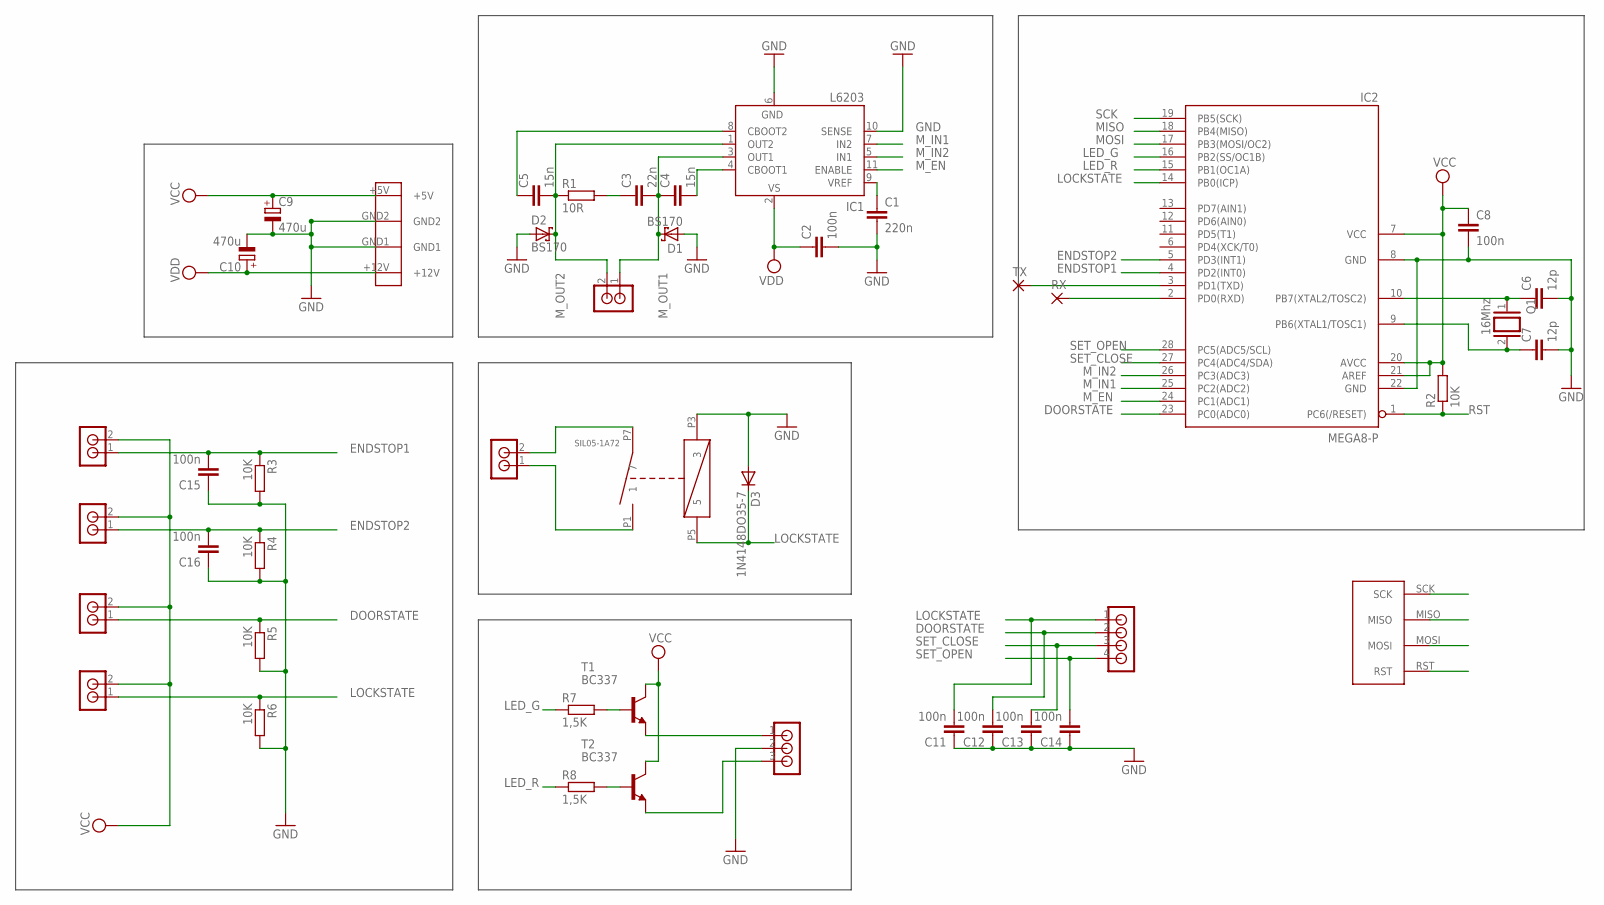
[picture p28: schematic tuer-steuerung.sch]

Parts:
C1: 220n; C025-024X044
C2, C8, C11, C12, C13, C14, C15, C16: 100n; C025-024X044
C3: 22n; C025-024X044
C4: 15n; C025-024X044
C5: 15n; C050-024X044
C6, C7: 12p; C050-025X075
C9, C10: 470u; TAP5-80
D1, D2: BS170; DO35-7
D3: 1N4148DO35-7; DO35-7
DOORSTATE: RIACON_101_2
ENDSTOP1, ENDSTOP2: RIACON_101_2
IC1: L6203; MULTIWATT-11
IC2: MEGA8-P; DIL28-3
LOCKSTATE: RIACON_101_2
MOTOR: RIACON_101_2
NERDSTERN: RIACON_101_2
Q1: 16Mhz; QS
R1: 10R; 0207/5V
R2, R3, R4, R5, R6: 10K; 0204/5
R7, R8: 1,5K; 0204/5
RX: 1,6/0,9
T1, T2: BC337; TO92
TX: 1,6/0,9
U$1: PSW_5
U$2: SIL05-1A72
U$3: AVR_ISP
U$4: RIACON_101_3
U$5: RIACON_101_4

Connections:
DOORSTATE: C12.2, DOORSTATE.1, IC2.23 (PC0(ADC0)), R5.1, U$5.2
ENDSTOP1: C15.2, ENDSTOP1.1, IC2.4 (PD2(INT0)), R3.1
ENDSTOP2: C16.2, ENDSTOP2.1, IC2.5 (PD3(INT1)), R4.1
GND: C1.2, C2.2, C6.2, C7.2, C8.2, C9.-, C10.-, C11.1, C12.1, C13.1, C14.1, C15.1, C16.1, D1.A, D2.A, D3.A, IC1.6 (GND), IC1.10 (SENSE), IC2.8 (GND), IC2.22 (GND), R3.2, R4.2, R5.2, R6.2, U$1.GND1, U$1.GND2, U$2.P3 (3), U$3.GND, U$4.2
LED_G: IC2.16 (PB2(SS/OC1B)), R7.1
LED_R: IC2.15 (PB1(OC1A)), R8.1
LOCKSTATE: C11.2, D3.C, IC2.14 (PB0(ICP)), LOCKSTATE.1, R6.1, U$2.P5 (5), U$5.1
MISO: IC2.18 (PB4(MISO)), U$3.MISO
MOSI: IC2.17 (PB3(MOSI/OC2)), U$3.MOSI
M_EN: IC1.11 (ENABLE), IC2.24 (PC1(ADC1))
M_IN1: IC1.7 (IN2), IC2.25 (PC2(ADC2))
M_IN2: IC1.5 (IN1), IC2.26 (PC3(ADC3))
M_OUT1: C3.2, C4.1, D1.C, IC1.3 (OUT1), MOTOR.1
M_OUT2: C5.2, D2.C, IC1.1 (OUT2), MOTOR.2, R1.1
unnamed: C6.1, IC2.10 (PB7(XTAL2/TOSC2)), Q1.1
unnamed: C7.1, IC2.9 (PB6(XTAL1/TOSC1)), Q1.2
unnamed: C1.1, IC1.9 (VREF)
unnamed: NERDSTERN.2, U$2.P7 (7)
unnamed: NERDSTERN.1, U$2.P1 (1)
unnamed: C3.1, R1.2
unnamed: C4.2, IC1.4 (CBOOT1)
unnamed: C5.1, IC1.8 (CBOOT2)
unnamed: R7.2, T1.2 (B)
unnamed: R8.2, T2.2 (B)
unnamed: T1.1 (E), U$4.1
unnamed: T2.1 (E), U$4.3
unnamed: IC2.3 (PD1(TXD)), TX.1
unnamed: IC2.2 (PD0(RXD)), RX.1
RST: IC2.1 (PC6(/RESET)), R2.1, U$3.RST
SCK: IC2.19 (PB5(SCK)), U$3.SCK
SET_CLOSE: C13.2, IC2.27 (PC4(ADC4/SDA)), U$5.3
SET_OPEN: C14.2, IC2.28 (PC5(ADC5/SCL)), U$5.4
VCC: C8.1, C9.+, DOORSTATE.2, ENDSTOP1.2, ENDSTOP2.2, IC2.7 (VCC), IC2.20 (AVCC), IC2.21 (AREF), LOCKSTATE.2, R2.2, T1.3 (C), T2.3 (C), U$1.+5V, U$3.VCC
VDD: C2.1, C10.+, IC1.2 (VS), U$1.+12V

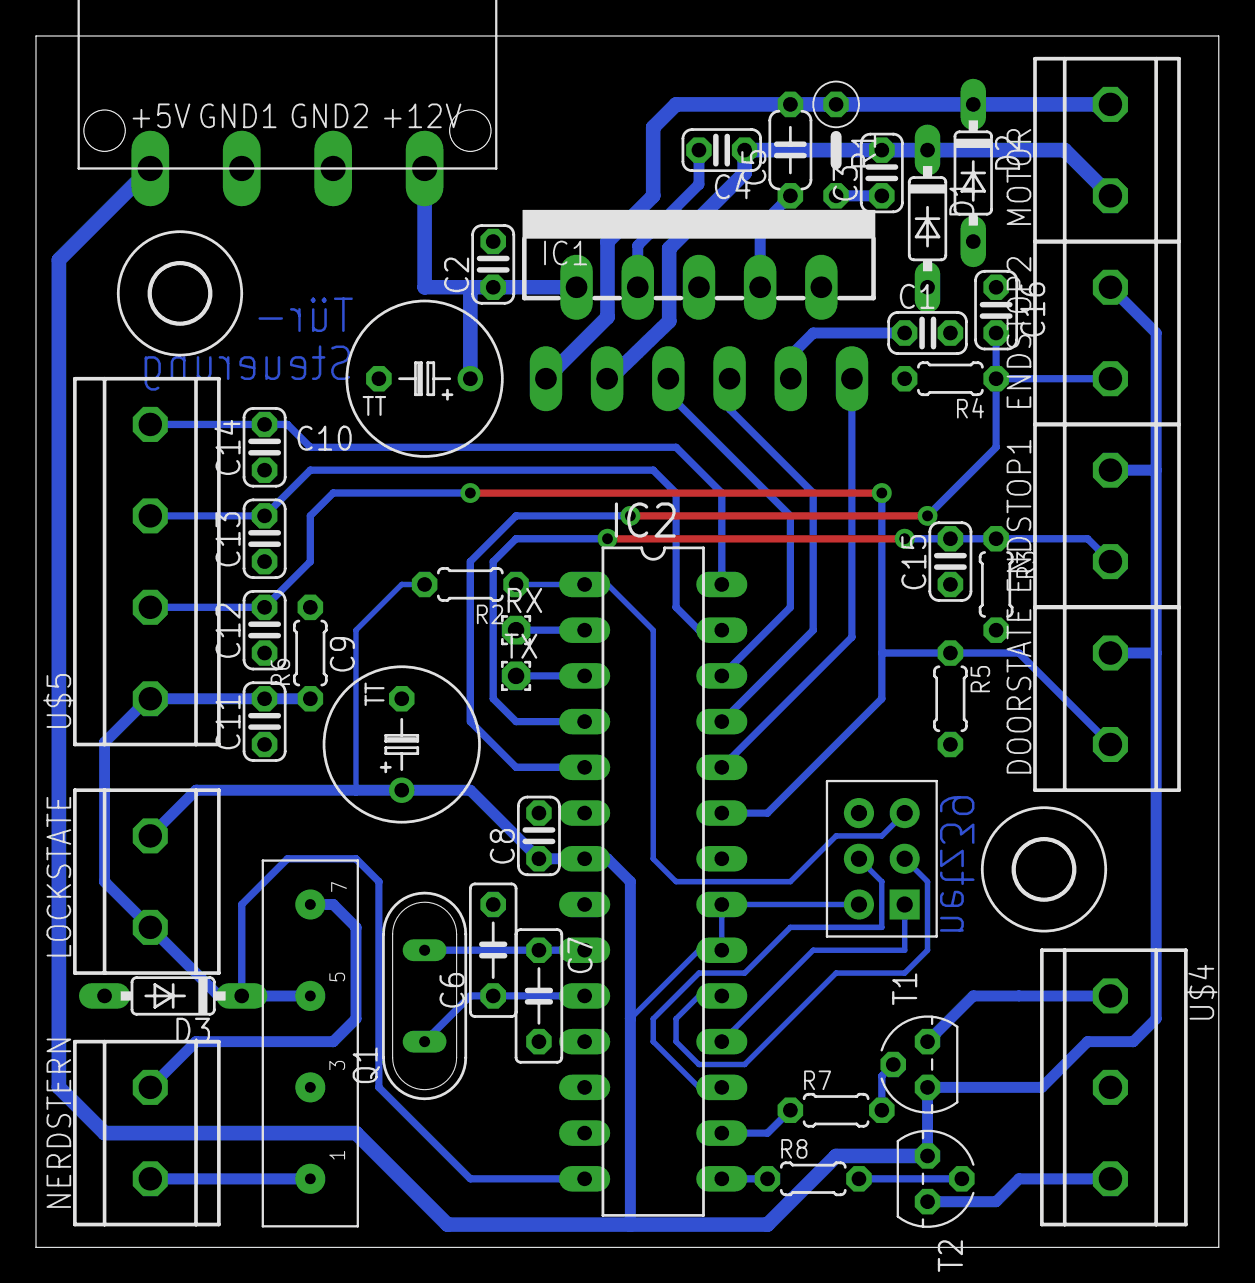
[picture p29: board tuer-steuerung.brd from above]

Board: 2 copper layers, 65.7 x 67.3 mm, 47 parts (0 on the bottom side), 34 nets.

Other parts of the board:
U$6, U$7: 3,2

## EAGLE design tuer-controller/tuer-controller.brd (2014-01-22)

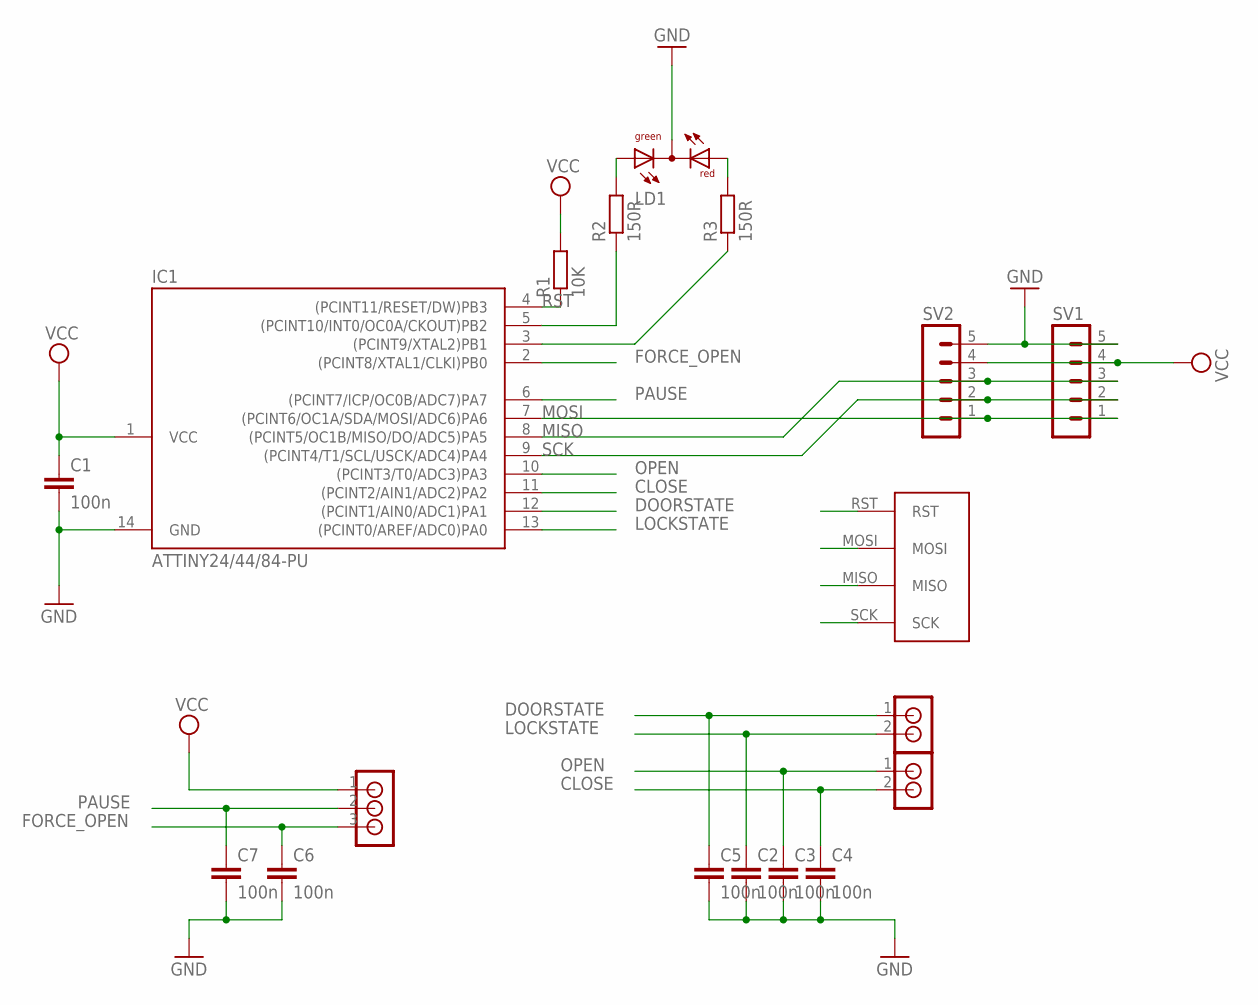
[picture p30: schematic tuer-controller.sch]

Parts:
C1, C2, C3, C4, C5, C6, C7: 100n; C025-024X044
IC1: ATTINY24/44/84-PU; DIL14
LD1: DUOLED-RG-C; DUOLED-C-5MM
R1: 10K; 0207/5V
R2: 150R; 0207/10
R3: 150R; 0207/15
SV1, SV2: MA05-1
U$1: AVR_ISP
U$2, U$3: RIACON_101_2
U$5: RIACON_59_3

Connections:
CLOSE: C4.1, IC1.11 ((PCINT2/AIN1/ADC2)PA2), U$3.2
DOORSTATE: C5.1, IC1.12 ((PCINT1/AIN0/ADC1)PA1), U$2.1
FORCE_OPEN: C6.1, IC1.2 ((PCINT8/XTAL1/CLKI)PB0), U$5.3
GND: C1.2, C2.2, C3.2, C4.2, C5.2, C6.2, C7.2, IC1.14 (GND), LD1.C, SV1.5, SV2.5, U$1.GND
LOCKSTATE: C2.1, IC1.13 ((PCINT0/AREF/ADC0)PA0), U$2.2
MISO: IC1.8 ((PCINT5/OC1B/MISO/DO/ADC5)PA5), SV1.3, SV2.3, U$1.MISO
MOSI: IC1.7 ((PCINT6/OC1A/SDA/MOSI/ADC6)PA6), SV1.1, SV2.1, U$1.MOSI
unnamed: IC1.5 ((PCINT10/INT0/OC0A/CKOUT)PB2), R2.1
unnamed: IC1.3 ((PCINT9/XTAL2)PB1), R3.1
unnamed: LD1.AX (AG), R2.2
unnamed: LD1.AR, R3.2
OPEN: C3.1, IC1.10 ((PCINT3/T0/ADC3)PA3), U$3.1
PAUSE: C7.1, IC1.6 ((PCINT7/ICP/OC0B/ADC7)PA7), U$5.2
RST: IC1.4 ((PCINT11/RESET/DW)PB3), R1.1, U$1.RST
SCK: IC1.9 ((PCINT4/T1/SCL/USCK/ADC4)PA4), SV1.2, SV2.2, U$1.SCK
VCC: C1.1, IC1.1 (VCC), R1.2, SV1.4, SV2.4, U$1.VCC, U$5.1

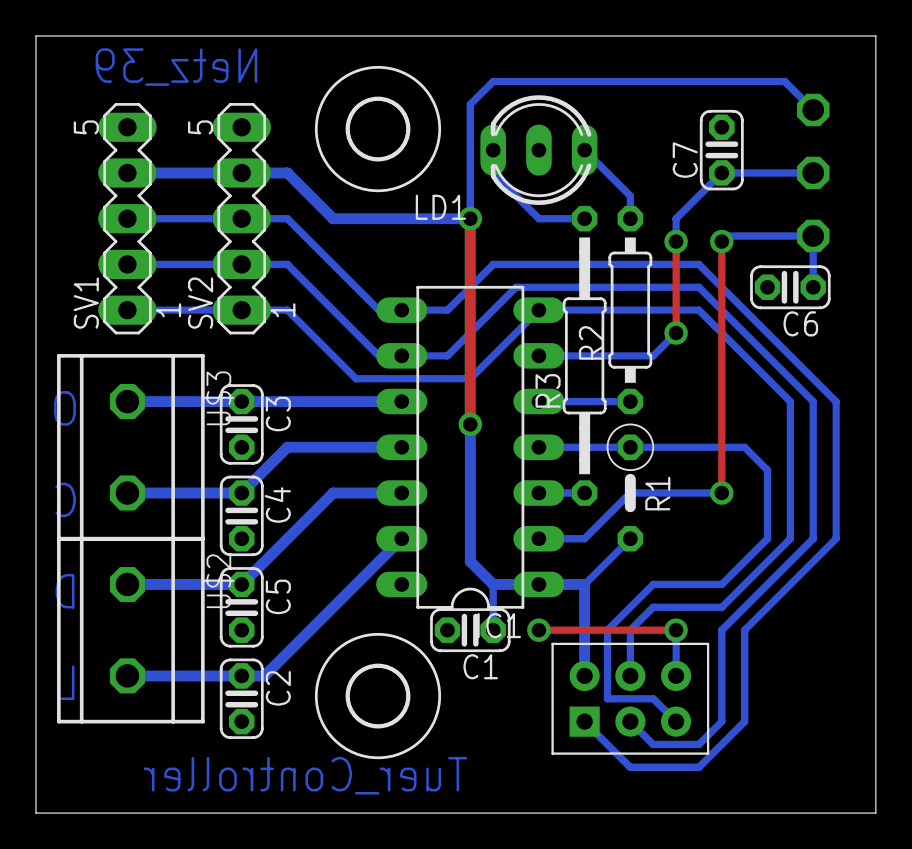
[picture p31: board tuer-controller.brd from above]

Board: 2 copper layers, 46.7 x 43.2 mm, 20 parts (1 on the bottom side), 16 nets.

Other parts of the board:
U$4, U$6: 3,2

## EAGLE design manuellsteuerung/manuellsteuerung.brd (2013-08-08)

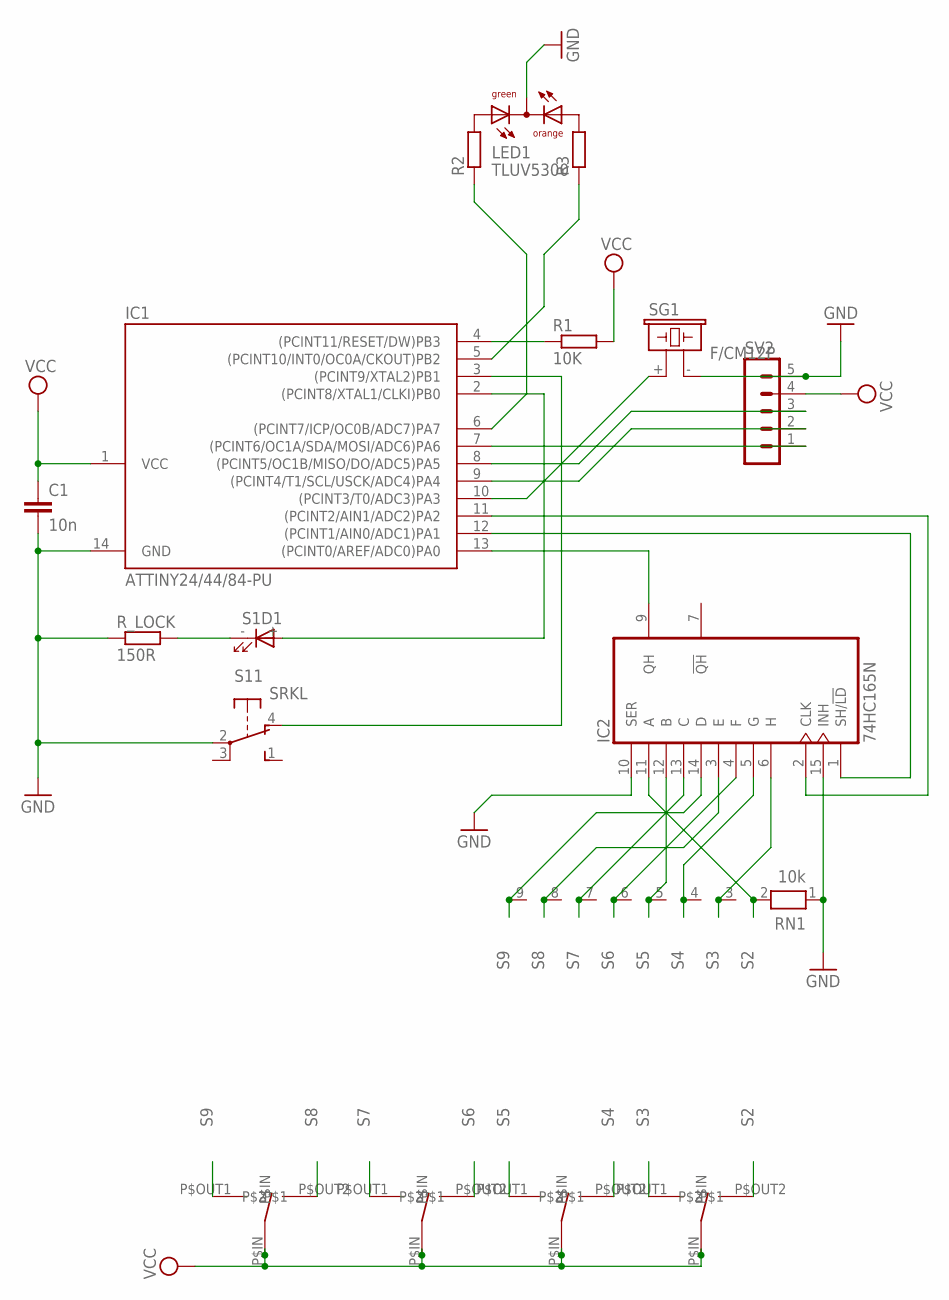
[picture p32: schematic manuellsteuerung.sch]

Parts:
C1: 10n; C025-024X044
IC1: ATTINY24/44/84-PU; DIL14
IC2: 74HC165N; DIL16
LED1: TLUV5300
R1: 10K; 0207/7
R2, R3: R-EU_0207/7; 0207/7
RN1: 10k; RN-9
R_LOCK: 150R; 0207/10
S1: SRKL
SG1: F/CM12P
SV2: MA05-1
U$1, U$2, U$3, U$4: MS_500E

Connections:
GND: C1.2, IC1.14 (GND), IC2.8 (GND), IC2.10 (SER), IC2.15 (INH), LED1.CC, RN1.1, R_LOCK.1, S1.2, SG1.- (2), SV2.5
MISO: IC1.8 ((PCINT5/OC1B/MISO/DO/ADC5)PA5), SV2.3
MOSI: IC1.7 ((PCINT6/OC1A/SDA/MOSI/ADC6)PA6), SV2.1
unnamed: IC1.13 ((PCINT0/AREF/ADC0)PA0), IC2.9 (QH)
unnamed: IC1.12 ((PCINT1/AIN0/ADC1)PA1), IC2.1 (SH/!LD)
unnamed: IC1.11 ((PCINT2/AIN1/ADC2)PA2), IC2.2 (CLK)
unnamed: R_LOCK.2, S1.- (C)
unnamed: IC1.2 ((PCINT8/XTAL1/CLKI)PB0), S1.+ (A)
unnamed: IC1.3 ((PCINT9/XTAL2)PB1), S1.4 (O)
unnamed: IC1.10 ((PCINT3/T0/ADC3)PA3), SG1.+ (1)
unnamed: LED1.AG, R2.2
unnamed: LED1.AO, R3.2
unnamed: IC1.6 ((PCINT7/ICP/OC0B/ADC7)PA7), R2.1
unnamed: IC1.5 ((PCINT10/INT0/OC0A/CKOUT)PB2), R3.1
RESET: IC1.4 ((PCINT11/RESET/DW)PB3), R1.1
S2: IC2.11 (A), RN1.2, U$4.P$OUT2
S3: IC2.6 (H), RN1.3, U$4.P$OUT1
S4: IC2.5 (G), RN1.4, U$1.P$OUT2
S5: IC2.12 (B), RN1.5, U$1.P$OUT1
S6: IC2.4 (F), RN1.6, U$3.P$OUT2
S7: IC2.13 (C), RN1.7, U$3.P$OUT1
S8: IC2.3 (E), RN1.8, U$2.P$OUT2
S9: IC2.14 (D), RN1.9, U$2.P$OUT1
SCK: IC1.9 ((PCINT4/T1/SCL/USCK/ADC4)PA4), SV2.2
VCC: C1.1, IC1.1 (VCC), IC2.16 (VCC), R1.2, SV2.4, U$1.P$IN, U$2.P$IN, U$3.P$IN, U$4.P$IN

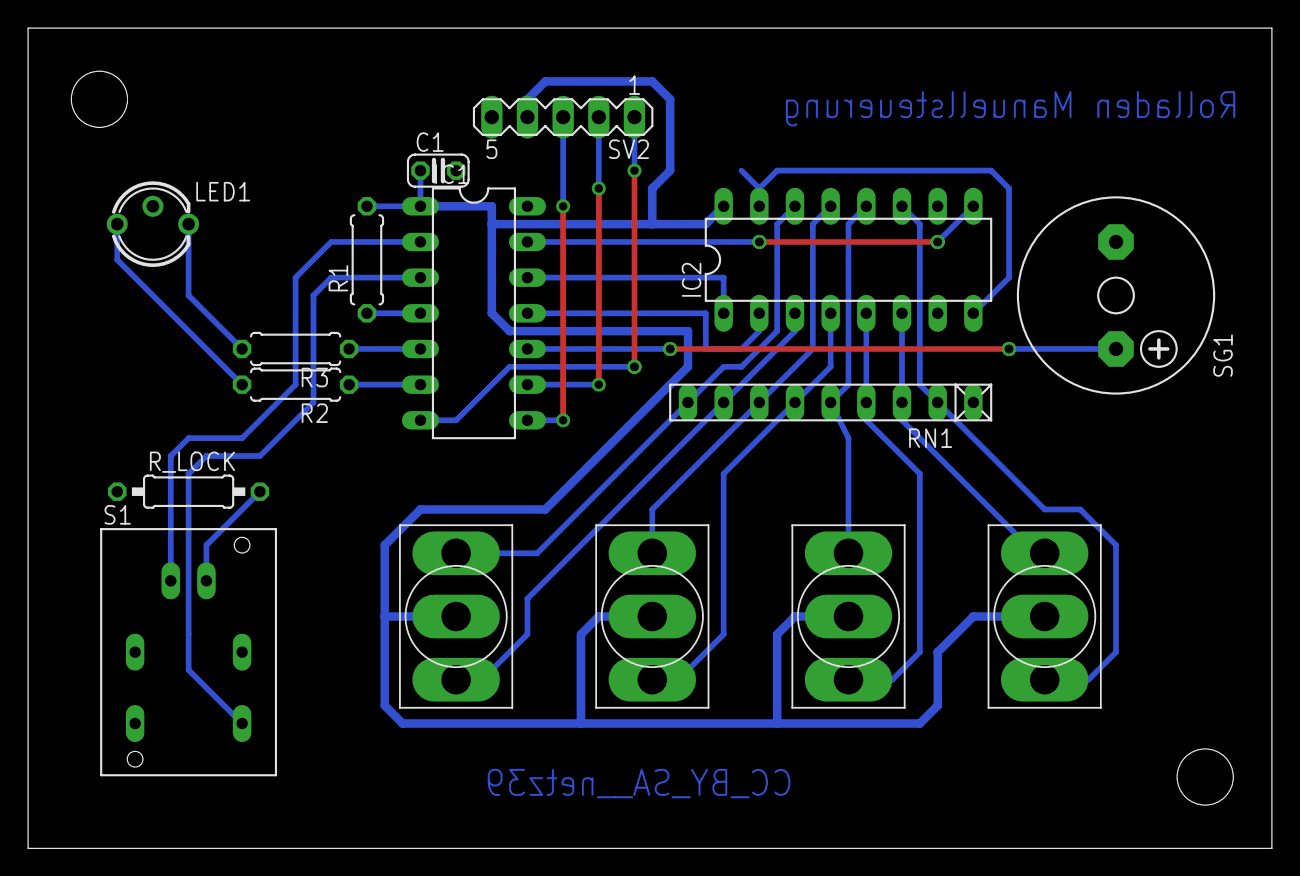
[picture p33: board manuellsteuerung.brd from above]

Board: 2 copper layers, 88.6 x 58.4 mm, 16 parts (0 on the bottom side), 25 nets.

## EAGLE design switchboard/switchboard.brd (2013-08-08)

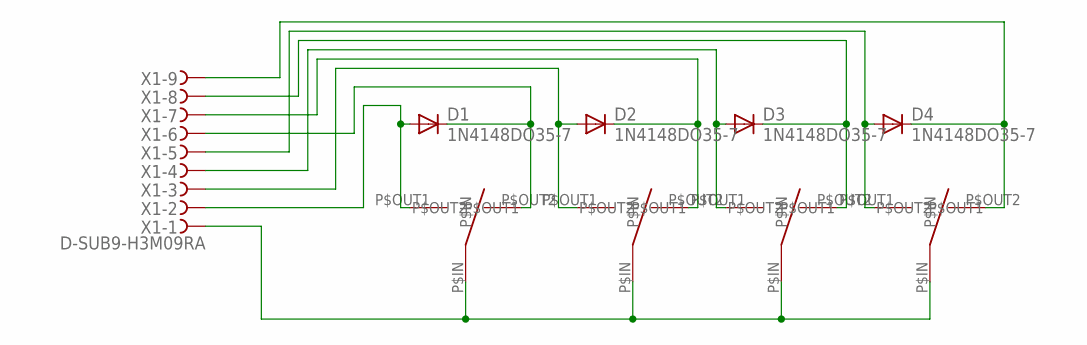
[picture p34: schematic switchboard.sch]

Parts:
D1, D2, D3, D4: 1N4148DO35-7; DO35-7
U$1, U$2, U$3, U$4: MS500E
X1: D-SUB9-H3M09RA; H3M09RA

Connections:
unnamed: D1.A, U$1.P$OUT1, X1.2
unnamed: D1.C, U$1.P$OUT2, X1.6
unnamed: D2.A, U$2.P$OUT1, X1.3
unnamed: D2.C, U$2.P$OUT2, X1.7
unnamed: D3.A, U$3.P$OUT1, X1.4
unnamed: D3.C, U$3.P$OUT2, X1.8
unnamed: D4.A, U$4.P$OUT1, X1.5
unnamed: D4.C, U$4.P$OUT2, X1.9
VCC: U$1.P$IN, U$2.P$IN, U$3.P$IN, U$4.P$IN, X1.1

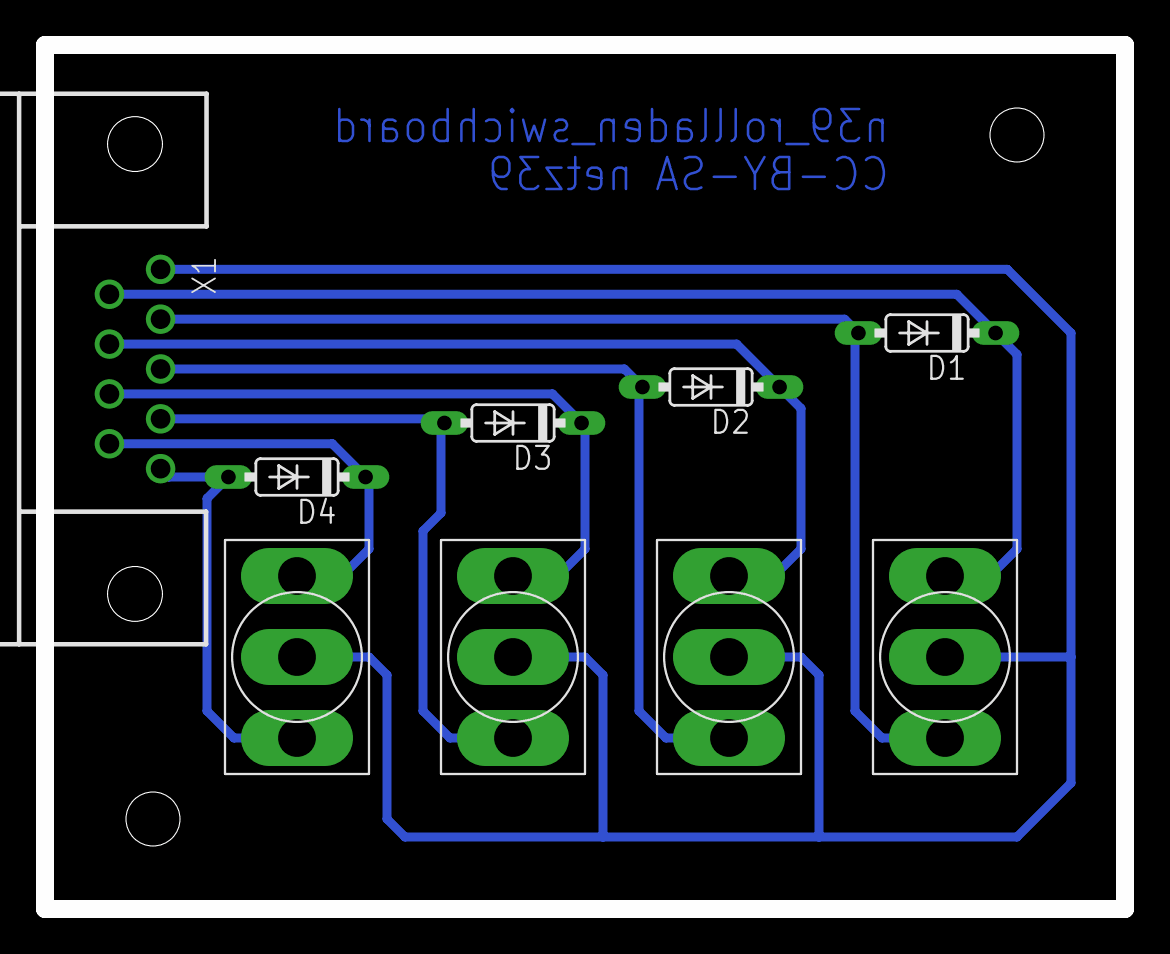
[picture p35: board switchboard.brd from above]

Board: 2 copper layers, 60.0 x 48.0 mm, 9 parts (0 on the bottom side), 9 nets.

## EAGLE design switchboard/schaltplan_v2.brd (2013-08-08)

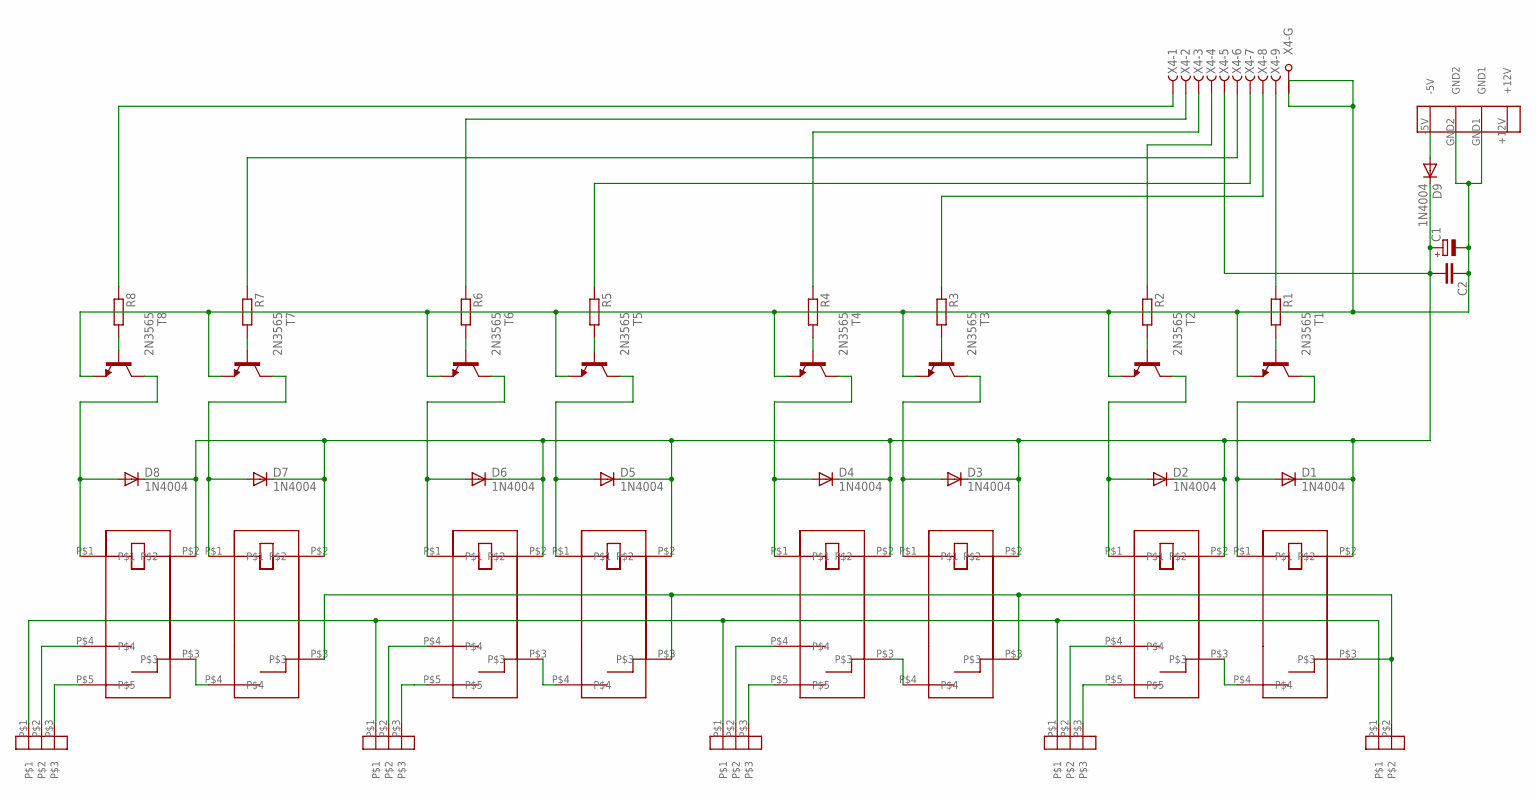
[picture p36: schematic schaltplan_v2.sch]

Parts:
C1: CPOL-EUE3.5-8; E3,5-8
C2: C-EU025-030X050; C025-030X050
D1, D2, D3, D4, D5, D6, D7, D8, D9: 1N4004; DO41-10
R1, R2, R3, R4, R5, R6, R7, R8: R-EU_0207/7; 0207/7
T1, T2, T3, T4, T5, T6, T7, T8: 2N3565; TO92
U$1, U$3, U$5, U$7: JS_05_MN_KT
U$2, U$4, U$6, U$8: JS_05_N_K
U$9: WAGO_734_262
U$10, U$11, U$12, U$13: WAGO_734_263
U$14: PSW_5
X4: F09HPS; F09HP

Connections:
GND: C1.-, C2.1, T1.3 (E), T2.3 (E), T3.3 (E), T4.3 (E), T5.3 (E), T6.3 (E), T7.3 (E), T8.3 (E), U$14.GND1, U$14.GND2, X4.G1, X4.G2
GND2: U$9.P$1, U$10.P$1, U$11.P$1, U$12.P$1, U$13.P$1
unnamed: U$2.P$5, U$10.P$3
unnamed: U$2.P$4, U$10.P$2
unnamed: U$1.P$4, U$2.P$3
unnamed: U$1.P$3, U$3.P$3, U$5.P$3, U$7.P$3, U$9.P$2
unnamed: D1.A, T1.1 (C), U$1.P$1
unnamed: D9.A, U$14.-5V
unnamed: R1.2, T1.2 (B)
unnamed: D2.A, T2.1 (C), U$2.P$1
unnamed: R5.1, X4.7 (F)
unnamed: D3.A, T3.1 (C), U$3.P$1
unnamed: R6.2, T6.2 (B)
unnamed: R6.1, X4.2 (F)
unnamed: R8.1, X4.1 (F)
unnamed: U$4.P$5, U$11.P$3
unnamed: U$4.P$4, U$11.P$2
unnamed: U$3.P$4, U$4.P$3
unnamed: D4.A, T4.1 (C), U$4.P$1
unnamed: R7.1, X4.6 (F)
unnamed: R3.2, T3.2 (B)
unnamed: R4.1, X4.3 (F)
unnamed: D5.A, T5.1 (C), U$5.P$1
unnamed: R2.1, X4.4 (F)
unnamed: R2.2, T2.2 (B)
unnamed: R4.2, T4.2 (B)
unnamed: U$6.P$5, U$12.P$3
unnamed: U$6.P$4, U$12.P$2
unnamed: U$5.P$4, U$6.P$3
unnamed: D6.A, T6.1 (C), U$6.P$1
unnamed: D7.A, T7.1 (C), U$7.P$1
unnamed: D8.A, T8.1 (C), U$8.P$1
unnamed: R5.2, T5.2 (B)
unnamed: R3.1, X4.8 (F)
unnamed: R1.1, X4.9 (F)
unnamed: R8.2, T8.2 (B)
unnamed: U$8.P$5, U$13.P$3
unnamed: U$8.P$4, U$13.P$2
unnamed: U$7.P$4, U$8.P$3
unnamed: R7.2, T7.2 (B)
V+: C1.+, C2.2, D1.C, D2.C, D3.C, D4.C, D5.C, D6.C, D7.C, D8.C, D9.C, U$1.P$2, U$2.P$2, U$3.P$2, U$4.P$2, U$5.P$2, U$6.P$2, U$7.P$2, U$8.P$2, X4.5 (F)

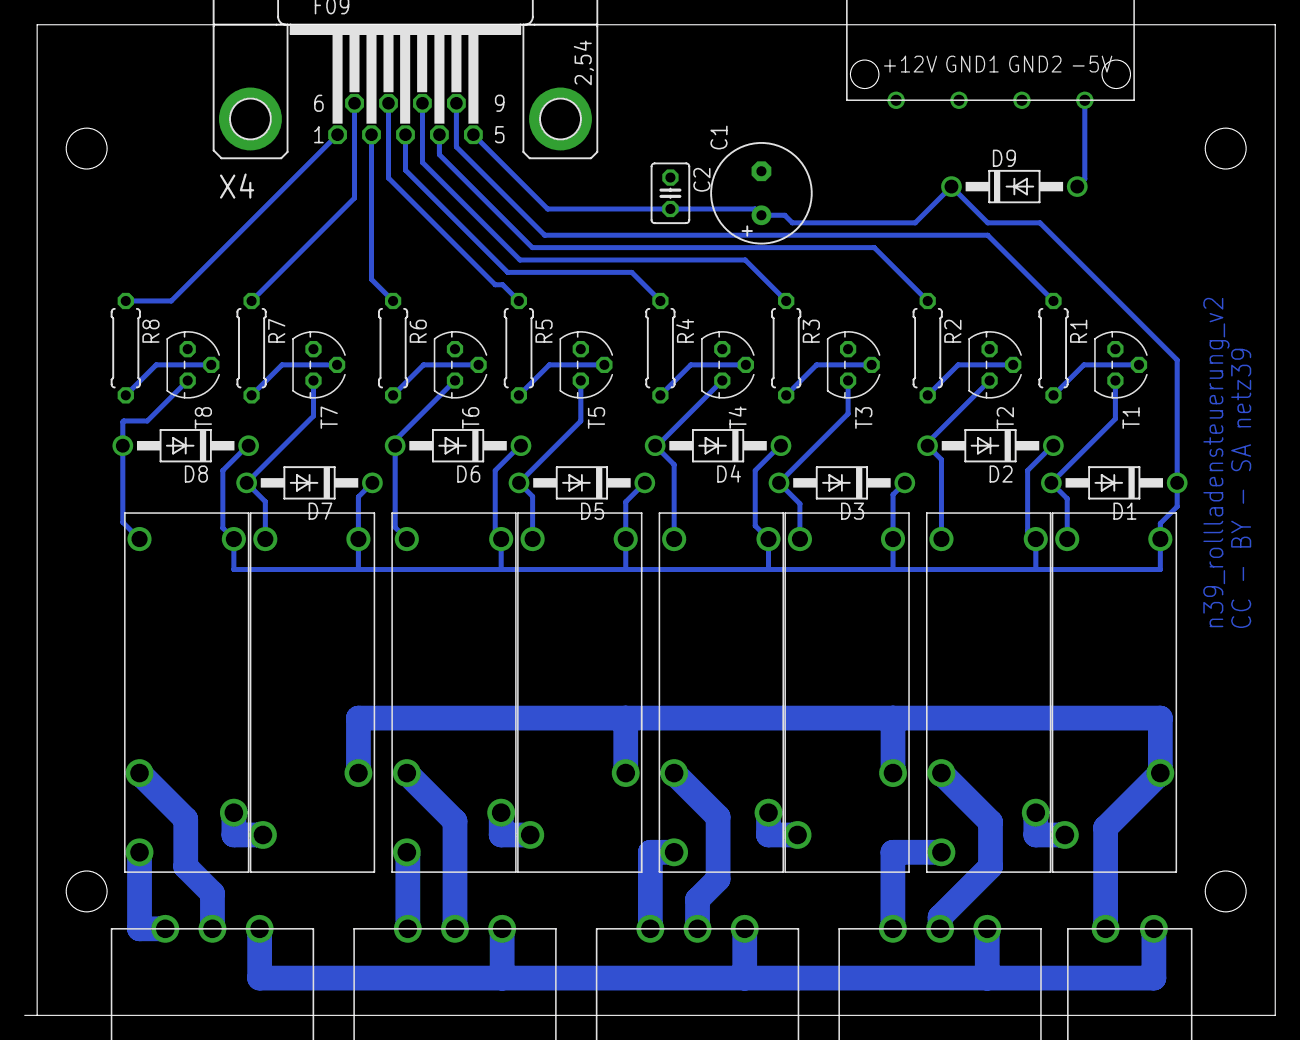
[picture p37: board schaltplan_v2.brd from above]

Board: 2 copper layers, 101.0 x 80.0 mm, 42 parts (0 on the bottom side), 41 nets.

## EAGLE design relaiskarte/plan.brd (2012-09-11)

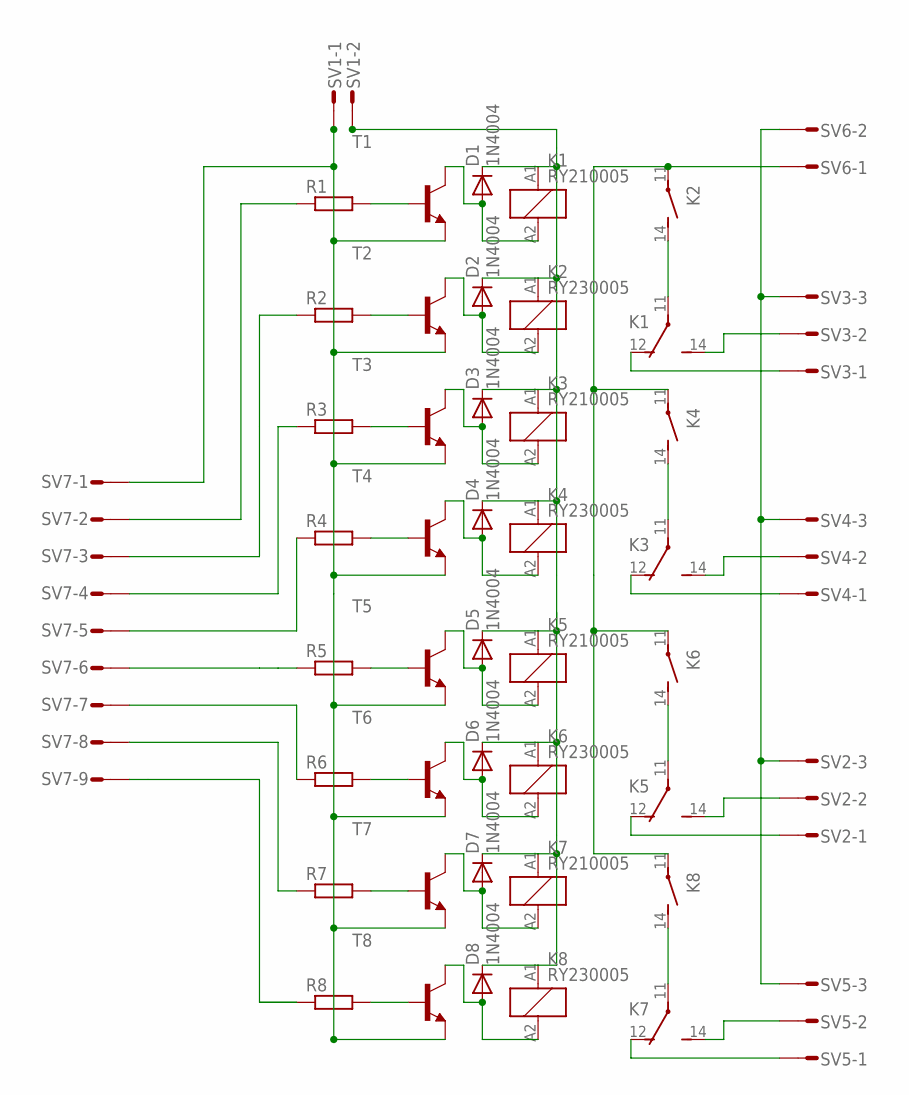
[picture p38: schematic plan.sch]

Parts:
D1, D2, D3, D4, D5, D6, D7, D8: 1N4004; DO41-10
K1, K3, K5, K7: RY210005; RY-II
K2, K4, K6, K8: RY230005; RY-II1
R1, R2, R3, R4, R5, R6, R7, R8: R-EU_0207/7; 0207/7
SV1, SV6: L02P
SV2, SV3, SV4, SV5: L03P
SV7: L09P
T1, T2, T3, T4, T5, T6, T7, T8: -NPN-TO92; TO92

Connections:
unnamed: R1.2, T1.2 (B)
unnamed: R2.2, T2.2 (B)
unnamed: SV1.1, SV7.1, T1.1 (E), T2.1 (E)
unnamed: R3.2, T3.2 (B)
unnamed: D1.A, K1.A2 (2), T1.3 (C)
unnamed: D2.A, K2.A2 (2), T2.3 (C)
unnamed: D1.C, D2.C, K1.A1 (1), K2.A1 (1), SV1.2
unnamed: R4.2, T4.2 (B)
unnamed: K1.11, K2.14 (S)
unnamed: SV2.3, SV3.3, SV4.3, SV5.3, SV6.2
unnamed: D3.A, K3.A2 (2), T3.3 (C)
unnamed: D4.A, K4.A2 (2), T4.3 (C)
unnamed: D3.C, D4.C, K3.A1 (1), K4.A1 (1)
unnamed: K3.11, K4.14 (S)
unnamed: K3.14 (S), SV4.2
unnamed: K3.12 (O), SV4.1
unnamed: K1.14 (S), SV3.2
unnamed: K1.12 (O), SV3.1
unnamed: K2.11, K4.11, K6.11, K8.11, SV6.1
unnamed: R1.1, SV7.2
unnamed: R5.2, T5.2 (B)
unnamed: R6.2, T6.2 (B)
unnamed: T3.1 (E), T4.1 (E), T5.1 (E), T6.1 (E)
unnamed: D5.A, K5.A2 (2), T5.3 (C)
unnamed: D6.A, K6.A2 (2), T6.3 (C)
unnamed: D5.C, D6.C, K5.A1 (1), K6.A1 (1)
unnamed: K5.11, K6.14 (S)
unnamed: R7.2, T7.2 (B)
unnamed: R8.2, T8.2 (B)
unnamed: T7.1 (E), T8.1 (E)
unnamed: D7.A, K7.A2 (2), T7.3 (C)
unnamed: D8.A, K8.A2 (2), T8.3 (C)
unnamed: D7.C, D8.C, K7.A1 (1), K8.A1 (1)
unnamed: K7.11, K8.14 (S)
unnamed: K7.14 (S), SV5.2
unnamed: K7.12 (O), SV5.1
unnamed: K5.14 (S), SV2.2
unnamed: K5.12 (O), SV2.1
unnamed: R8.1, SV7.9
unnamed: R6.1, SV7.7
unnamed: R5.1, SV7.6
unnamed: R4.1, SV7.5
unnamed: R3.1, SV7.4
unnamed: R2.1, SV7.3
unnamed: R7.1, SV7.8


Board: 2 copper layers, 100.0 x 80.0 mm, 39 parts (1 on the bottom side), 45 nets.

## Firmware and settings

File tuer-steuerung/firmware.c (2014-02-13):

/*
 * Tür-Steuerung
 * Autor: Stefan Haun <tux@netz39.de>
 * 
 * Entwickelt für ATMEGA8
 * 
 * DO NOT forget to set the fuses s.th. the controller uses a 16 MHz external oscillator clock!
 */


/* define CPU frequency in MHz here if not defined in Makefile */
#ifndef F_CPU
#define F_CPU 16000000UL
#endif

#include <avr/io.h>
#include <avr/interrupt.h>
#include <util/delay.h>
#include <stdint.h>


/// Port Helper Macros
#define setPortB(mask)   (PORTB |= (mask))
#define resetPortB(mask) (PORTB &= ~(mask))
#define setPortC(mask)   (PORTC |= (mask))
#define resetPortC(mask) (PORTC &= ~(mask))
#define setPortD(mask)   (PORTD |= (mask))
#define resetPortD(mask) (PORTD &= ~(mask))

/// Eingänge

// Endstop-Schalter
#define isEndstopClose   (((PIND & (1<<PD2)) == (1<<PD2)) ? 1 : 0)
#define isEndstopOpen    (((PIND & (1<<PD3)) == (1<<PD3)) ? 1 : 0)

// Command-Eingänge (invertiert!)
#define isSetClose       (((PINC & (1<<PC4)) == (1<<PC4)) ? 0 : 1)
#define isSetOpen        (((PINC & (1<<PC5)) == (1<<PC5)) ? 0 : 1)

// Türschloss
#define isLockOpen       (((PINB & (1<<PB0)) == (1<<PB0)) ? 1 : 0)

// Türstatus
#define isDoorClosed     (((PINC & (1<<PC0)) == (1<<PC0)) ? 1 : 0)


/// Motor-Funktionen

// Status Motor-Ansteuerung zurückgeben
#define isHBridgeActive  (((PINC & (1<<PC1)) == (1<<PC1)) ? 1 : 0)
#define isMotorOpen      (((PINC & (1<<PC2)) == (1<<PC2)) ? 1 : 0)
#define isMotorClose     (((PINC & (1<<PC3)) == (1<<PC3)) ? 1 : 0)

/*
 * Block-Counter für den Motor.
 * Wird vom Timer decrementiert. Nur wenn == 0 kann das Schloss abgeschlossen
 * werden.
 */
static char isBlocked = 0;

/*
 * Motor anhalten!
 */
void stopMotor() {
  resetPortC((1 << PC2) | (1 << PC3));
  // aktives Bremsen passiert nur, wenn die H-Brücke aktiviert ist
  // -> Enable 250ms später löschen
  _delay_ms(250);
  resetPortC((1 << PC1));
}

/*
 * Motor für einen bestimmten Zeitraum blockieren.
 */
void blockMotor() {
  isBlocked = 100;
}

/*
 * Motor-Stellung und Schalter prüfen, ggf. Motor stoppen.
 */
void checkMotor() {
  // Fall: Motor "auf"
  if (isMotorOpen) {
    // Motor darf nur "auf" drehen, wenn der Auf-Endstop nicht erreicht ist
    if (isEndstopOpen)
      stopMotor();
  }
  
  // Fall: Motor "zu"
  if (isMotorClose) {
    // schließen nur bei geschlossener Tür
    if (!isDoorClosed || isBlocked)
      stopMotor();
    
    // Motor darf nur "zu" drehen, wenn der Zu-Endstop nicht erreicht ist
    if (isEndstopClose)
      stopMotor();
    
    // fertig, wenn das Schloss nicht mehr offen ist
    if (!isLockOpen)
      stopMotor();    
  }  
}

/*
 * Motor starten
 * direction      Drehrichtung "zu" oder "auf"
 * siehe Konstanten unter diesem Kommentar
 */
#define MOTOR_CLOSE 1
#define MOTOR_OPEN  2
void startMotor(const char direction) {
  // Motor Close
  if (direction == MOTOR_CLOSE) {
    // endstop close darf nicht aktiv sein, Schloss muss offen sein und Tür muss geschlossen sein
    if (!isEndstopClose && isLockOpen && isDoorClosed && !isBlocked) {
      // Richtung einstellen
      resetPortC(1 << PC2);
      setPortC(1 << PC3);
      // H-Brücke aktivieren
      setPortC(1 << PC1);
    }
  }

  // Motor Open
  if (direction == MOTOR_OPEN) {
    // endstop open darf nicht aktiv sein
    if (!isEndstopOpen) {
      // Richtung einstellen
      resetPortC(1 << PC3);
      setPortC(1 << PC2);
      // H-Brücke aktivieren
      setPortC(1 << PC1);
    }
  }

  // abschließender Check
  checkMotor();
}


/// Anzeige-Funktionen (LED)

// Status
/*
 * Bits 0,1 rot
 * Bits 2,3 grün
 */

#define LED_OFF  0b00
#define LED_SLOW 0b01
#define LED_FAST 0b10
#define LED_ON   0b11

#define GET_RED     (LEDstatus & 0b0011)
#define GET_GREEN   ((LEDstatus & 0b1100) >> 2)

static char LEDstatus = 0;

/*
 * Farbanzeige (LED) setzen oder löschen
 * 
 * col      Farbe
 * state    Status an/aus
 * siehe Konstanten unter diesem Kommentar
 */
#define COL_RED   1
#define COL_GREEN 2
#define COL_OFF   0
#define COL_ON    1
void color(const char col, const char state) {
  const char mask = 1 << (col);
  if (state)
    setPortB(mask);
  else
    resetPortB(mask);
}

void setLED(const char col, const char state) {
  if (col == COL_RED) {
    LEDstatus &= ~(0b0011);
    LEDstatus |= state;
  }
  if (col == COL_GREEN) {
    LEDstatus &= ~(0b1100);
    LEDstatus |= (state<<2);
  }
}

/// Zustand

/*
 * Prüfen, ob das Schloss komplett geöffnet ist
 * Return: 0, wenn noch nicht komplett geöffnet, sonst ungleich 0
 */
char isFullyOpen() {
  // komplett geöffnet, wenn der Endstop erreicht ist
  return isEndstopOpen;
}

/*
 * Prüfen, ob das Schloss komplett geschlossen ist
 * Return: 0, wenn noch nicht komplett geschlossen, sonst ungleich 0
 */
char isFullyClosed() {
  // komplett geschlossen, wenn der Endstop erreicht 
  // oder das Schloss nicht mehr offen ist
  return isEndstopClose || !isLockOpen;
}


/// Infrastruktur

void init(void) {
  /*
   * Pin-Config PortB:
   *   PB0: IN	Lockstate
   *   PB1: OUT	LED_R
   *   PB2: OUT LED_G
   *   PB3: MOSI
   *   PB4: MISO
   *   PB5: SCK
   * 
   * Pin-Config PortC:
   *   PC0: IN	Doorstate
   *   PC1: OUT	M_EN (Motor enable)
   *   PC2: OUT	M_IN1 (Motor Input direction 1)
   *   PC3: OUT	M_IN2 (Motor Input direction 2)
   *   PC4: IN	SET_CLOSE
   *   PC5: IN	SET_OPEN
   * 
   * Pin-Config PortD:
   *   PD0: RXD
   *   PD1; TXD
   *   PD2: IN	Endstop 1, Closed (INT0)
   *   PD3: IN	Endstop 2, Open   (INT1)
   */
  
  DDRB  = 0b00000110;
  // PullUp für Eingänge
  PORTB = 0b00000000;

  DDRC  = 0b00001110;
  // PullUp für Eingänge
  PORTC = 0b00110000;

  DDRD  = 0b00000000;
  // PullUp für Eingänge
  PORTD = 0b00000000;

   /*  disable interrupts  */
   cli();
   
   // Interrupts einstellen
   // interrupt bei Pegelwechsel
   
   // PD2 -> INT0
   MCUCR |= (1 << ISC00); // | (1 << ISC01);
   // PD3 -> INT1
   MCUCR |= (1 << ISC10); // | (1 << ISC11);
   
   // aktivieren
   GICR |= (1 << INT0) | (1 << INT1);

   
   /*  set clock   */
  
  // prescaler 1024, CTC
  TCCR1A = 0;
  TCCR1B = (1 << WGM12) | (1 << CS02) | (1 << CS00);

  // vergleichswert
  OCR1A = 0xff;
  
  // aktivieren
  TIMSK |= (1 << OCIE1A);
    
  
  
  // Global Interrupts aktivieren
  sei();  
}

int main(void)
{
  // initialisieren
  init();

  // Bereit-Meldung
  _delay_ms(250);
  setLED(COL_RED, LED_FAST);
  _delay_ms(1000);
  setLED(COL_RED, LED_OFF);
  setLED(COL_GREEN, LED_FAST);
  _delay_ms(700);
  setLED(COL_GREEN, LED_OFF);
  
  
  while(1) {
    checkMotor();

    // bei offener Tür immer auch das Schloss öffnen!
    if (!isDoorClosed && !isFullyOpen()) {
      startMotor(MOTOR_OPEN);
      blockMotor();
    }
    else if (isSetOpen) {
      startMotor(MOTOR_OPEN);
    }
    else if (isSetClose) {
      startMotor(MOTOR_CLOSE);
    } else if (!isDoorClosed && !isFullyOpen()) {
      // bei unklarem Status: tür auf
      startMotor(MOTOR_OPEN);
    }
  
    // Es wird nur einer der Stati rot/grün angezeigt, 
    // wenn die Tür "geschlossen" signalisiert, wird rot bevorzugt,
    // bei gleichzeitigem "offen"-status blinkt grün schnell
    // (dann liegt ein unzulässiger Zustand vor).

    // grün blinken, wenn Motor Richtung "auf"
    if (isMotorOpen)
      setLED(COL_GREEN, LED_SLOW);
    // grün, wenn komplett offen, sonst aus
    else if (isFullyOpen())
      setLED(COL_GREEN, isFullyClosed() ? LED_FAST : LED_ON);
//      setLED(COL_GREEN, isFullyClosed() ? LED_OFF : LED_ON);
    else
      setLED(COL_GREEN, LED_OFF);
    
    // rot blinken, wenn Motor Richtung "zu"
    if (isMotorClose)
      setLED(COL_RED, LED_SLOW);
    // rot, wenn komplett geschlossen, sonst aus
    else
      setLED(COL_RED, isFullyClosed() ?  LED_ON : LED_OFF);
  
    
    
  } // while
  
  return 0;
}



/// Interrupt-Vektoren

volatile uint8_t blink = 0;
volatile uint8_t phase = 0;
ISR (TIMER1_COMPA_vect)
{
  // store state and disable interrupts
  const uint8_t _sreg = SREG;
  cli();
  
  // decrease the motor block counter
  if ((isBlocked > 0) && isDoorClosed)
    isBlocked--;

  // another motor check here
  checkMotor();
  
  // LED setting

  // red led
  const char rst = GET_RED;
  
  if (rst == LED_ON)
    color(COL_RED, COL_ON);
  else if (rst == LED_OFF)
    color(COL_RED, COL_OFF);

  // green led
  const char gst = GET_GREEN;
  if (gst == LED_ON)
    color(COL_GREEN, COL_ON);
  else if (gst == LED_OFF)
    color(COL_GREEN, COL_OFF);

  // anything blinking
  blink++;
  if (blink > 10) {
    blink = 0;
    phase++;
  
    if (phase > 3)
      phase = 0;

    if (rst == LED_SLOW)
      color(COL_RED, phase>1);
    else if (rst == LED_FAST)
      color(COL_RED, phase%2);
  
    if (gst == LED_SLOW)
      color(COL_GREEN, phase>1);
    else if (gst == LED_FAST)
      color(COL_GREEN, phase%2);
  } // blink


  // restore state
  SREG = _sreg;  
}

ISR (INT0_vect) {
  // store state and disable interrupts
  const uint8_t _sreg = SREG;
  cli();
    
  checkMotor();

  // restore state
  SREG = _sreg;
}

ISR (INT1_vect) {
  // store state and disable interrupts
  const uint8_t _sreg = SREG;
  cli();

  checkMotor();

  // restore state
  SREG = _sreg;
}

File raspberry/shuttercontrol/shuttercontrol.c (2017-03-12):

#include <stdlib.h>
#include <stdio.h>
#include <errno.h>
#include <unistd.h>
#include <string.h>

#include <time.h>
#include <syslog.h>

#include <wiringPi.h>
#include <wiringPiI2C.h>

#include <mosquitto.h>

#define I2C_ADDR_CONTROLLER 0x21
#define I2C_ADDR_MANUAL     0x22

const char* MQTT_HOST   = "platon";
const int   MQTT_PORT   = 1883;
const char* MQTT_TOPIC  = "Netz39/Things/Shuttercontrol/Button/Events";

#define MQTT_MSG_MAXLEN           16
const char* MQTT_MSG_BTNPRESS   = "button pressed";
const char* MQTT_MSG_NONE       = "none";

/**
 * Get the milliseconds since epoch.
 */
long current_millis() {
  struct timeval tv;
  gettimeofday(&tv, 0);
  
  return tv.tv_sec*1000L + tv.tv_usec/1000L;
}

///// I2C stuff /////

/**
  * This record contains the I2C file descriptors we use in this program
  */
struct I2C_descriptors {
  int controller;
  int manual;
} I2C_fd;

#define I2C_FD_CONTROLLER (I2C_fd.controller)
#define I2C_FD_MANUAL     (I2C_fd.manual)

/**
  * Initialize an I2C channel to the specified address. Exits with an error
  * message if the initialization fails,
  *
  * @param addr The target address.
  * @return File Descriptor for the I2C channel
  */
int I2C_setup_fd(const int addr) {
  const int fd = wiringPiI2CSetup(addr);
  if (!fd) {
    syslog(LOG_EMERG, "Error %d on I2C initialization!", errno);
    exit(-1);
  }
  return fd;
}

/**
  * Initialize all I2C channels and store the file descriptors.
  */
void I2C_init(void) {
  I2C_fd.controller = I2C_setup_fd(I2C_ADDR_CONTROLLER);
  I2C_fd.manual     = I2C_setup_fd(I2C_ADDR_MANUAL);
}

#define I2C_ERR_INVALIDARGUMENT -2

  union I2C_result {
    unsigned char c[2];
    unsigned short r;
  };


int I2C_command(const int fd, const char command, const char data) {
  // check parameter range
  if ((command < 0) || (command > 0x07))
    return I2C_ERR_INVALIDARGUMENT;
  if ((data < 0) || (data > 0x0f))
    return I2C_ERR_INVALIDARGUMENT;
  
  // TODO check fd
  
    
  // build the I2C data byte
  // arguments have been checked, 
  // this cannot be negative or more than 8 bits
  unsigned char send = (command << 4) + data; 
  
  // calculate the parity
  char v = send;
  char c;
  for (c = 0; v; c++) 
    v &= v-1;
  c &= 1;

  // set parity bit  
  send += (c << 7);
  
  union I2C_result result;
  result.r = 0;

  // maximal number of tries
  int hops=20;

  // try for hops times until the result is not zero
  while (!result.c[0] && --hops) {
    // send command
    result.r = wiringPiI2CReadReg16(fd, send);

    // check for transmission errors: 2nd byte is inverted 1st byte
    const unsigned char c = ~result.c[0];
    if (result.c[1] != c) 
      // if no match, reset the result
      result.r = 0;
  }
  
  if (!hops)
    syslog(LOG_DEBUG, "Giving up transmission!\n");
  
  return result.c[0];
}

///// I3C stuff /////

void I3C_reset_manual() {
  I2C_command(I2C_FD_MANUAL, 0x4, 0x0);
}

///// Manual Controll unit /////

#define SWITCH_UP      1
#define SWITCH_NEUTRAL 3
#define SWITCH_DOWN    2
#define SWITCH_LOCKED  0

#define SWITCH_ERR             -1
#define SWITCH_ERR_OUTOFBOUNDS -2

/**
  * Read the state of the specified switch.
  * @return 
  *	Switch state according to SWITCH_XXX, SWITCH_ERR if an error
  *	occurred.
  */
char read_switch_state(const char idx) {
  // check parameter range
  if ((idx < 1) || (idx > 4))
    return SWITCH_ERR_OUTOFBOUNDS;

  // send the command    
  const char state = I2C_command(I2C_FD_MANUAL, 0x3, idx);
  
  // return result
  return state;  
}

/**
  * Beep in the provided pattern.
  * @param The beep pattern. Only the last 4 Bits are evaluated!
  */
void beep(const char pattern) {
  I2C_command(I2C_FD_MANUAL, 0x1, pattern&0xf);
}

#define LED_PATTERN_OFF  0x00
#define LED_PATTERN_SLOW 0x01
#define LED_PATTERN_FAST 0x02
#define LED_PATTERN_ON   0x03

/**
  * Set manual mode LED to the specified blink pattern.
  * @param pattern The blink pattern; one of LED_PATTERN_XXX.
  */
void set_manual_mode_led(const char pattern) {
  I2C_command(I2C_FD_MANUAL, 0x2, pattern);
}

char get_manual_mode() {
  return I2C_command(I2C_FD_MANUAL, 0x5, 0);
}

#define MANUAL_MODE_ON  1
#define MANUAL_MODE_OFF 2

void set_manual_mode(const char mode) {
  I2C_command(I2C_FD_MANUAL, 0x5, mode);
}

///// Shutter Control unit /////

#define SHUTTER_ERR             -1
#define SHUTTER_ERR_OUTOFBOUNDS -2

#define SHUTTER_OFF  0
#define SHUTTER_UP   1
#define SHUTTER_DOWN 2

/**
  * Set the shutter control state.
  * @param idx Number of the shutter, between 1 and 4
  * @param state One of SHUTTER_XXX.
  * @return 0 if everything is okay, otherwise one of SHUTTER_ERR_XXX
  */
char set_shutter_state(const char idx, const char state) {
  // check parameter range
  if ((idx < 1) || (idx > 4))
    return SHUTTER_ERR_OUTOFBOUNDS;
  if ((state < 0) || (state > 2))
    return SHUTTER_ERR_OUTOFBOUNDS;  

  // determine the command
  char command = 0x0;
  switch (state) {
    case SHUTTER_OFF:  command = 0x1; break;
    case SHUTTER_UP:   command = 0x2; break;
    case SHUTTER_DOWN: command = 0x3; break;
    default: {
      syslog(LOG_EMERG, "set_shutter_state: Unknown shutter state: %d.");
      syslog(LOG_EMERG, "This cannot happen! Aborting with assertion error.");
      exit(-1);
    }
  }

  // send the command    
  I2C_command(I2C_FD_CONTROLLER, command, idx-1);

  // return OK
  return 0;
}

/**
  * Stop all the shutters!
  */
void stop_all_shutters() {
  I2C_command(I2C_FD_CONTROLLER, 0x0, 0x0);
}


char switch_state[4];
long switch_lastchange[4];

/**
  * Set stored switch states to NEUTRAL.
  */
void clear_stored_switch_state() {
  const long t = current_millis();
  int i;
  for (i=0; i < 4; i++) {
    switch_state[i] = SWITCH_NEUTRAL;
    switch_lastchange[i] = t;
  }
}

/**
  * Store a new switch state.
  * Return old state if there was a change.
  * @return the old state or 0 if there was no change
  */
char store_switch_state(const char idx, const char state) {
  const char old_state = switch_state[idx-1];
  
  if (old_state == state)
    return 0;

  switch_lastchange[idx-1] = current_millis();  
    
  switch_state[idx-1] = state;
  return old_state;
}
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

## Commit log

2012-09-11 initial commit of schematics
    [plan.brd, plan.sch]
2012-09-16 added schaltplan_v2
    [schaltplan_v2.brd, schaltplan_v2.sch]
2012-09-16 layout/board redesign
    [schaltplan_v2.brd, schaltplan_v2.sch]
2012-09-17 schaltplan_v2 finalized
    [schaltplan_v2.brd, schaltplan_v2.sch]
2012-09-17 more fixes
    [schaltplan_v2.brd, schaltplan_v2.sch]
2012-11-24 change 9pin connector to sub-d
    [schaltplan_v2.brd, schaltplan_v2.sch]
2013-01-01 initial schematic commit, copy from old repo
    [schaltplan_v2.brd, schaltplan_v2.sch]
2013-01-02 added correct connectors
    [schaltplan_v2.brd, schaltplan_v2.sch]
2013-01-02 replaced another connector
    [schaltplan_v2.brd, schaltplan_v2.sch]
2013-01-03 more layout fixes
    [schaltplan_v2.brd, schaltplan_v2.sch]
2013-01-03 wiring fix
    [schaltplan_v2.brd]
2013-01-03 fixed ground areas
    [schaltplan_v2.brd, schaltplan_v2.sch]
2013-01-27 minor layout fixes
    [schaltplan_v2.brd, schaltplan_v2.sch]
2013-01-27 just another fix
    [schaltplan_v2.brd]
2013-01-28 24367dfa: add drill holes and replace changed relais
    [schaltplan_v2.brd, schaltplan_v2.sch]
2013-01-28 24367dfa: add label text
    [schaltplan_v2.brd]
2013-01-28 minor fixes again
    [schaltplan_v2.brd]
2013-01-30 rerouting and fixed drill hole distances
    [schaltplan_v2.brd]
2013-01-31 fix ERC issues and schematic, reroute some signals
    overall connection was lost due to some signal renamings, some parts
    were not connected at all. additionally added restrict area around drill
    holes
    [schaltplan_v2.brd, schaltplan_v2.sch]
2013-01-31 fix wrong connections in schematics
    transitor pins were connected wrong and resistors are not diodes!
    [schaltplan_v2.brd, schaltplan_v2.sch]
2013-02-05 fix some paths on hv part
    [schaltplan_v2.brd]
2013-03-01 change label
    [schaltplan_v2.brd]
2013-03-03 add swichboard schematic and board
    [swichboard.brd, swichboard.sch]
2013-03-03 add text/drillholes/copper fill to swichboard
    [swichboard.brd]
2013-05-22 Relaiskarte in Unterordner verschoben
    [plan.brd, plan.sch, schaltplan_v2.brd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]
2013-05-25 Controller Schematics Controller-Boeard erster entwurf
    [controller.brd, controller.sch]
2013-05-25 Routing erster Versuch
    [controller.brd, controller.sch]
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2013-05-26 PLatinenlayout fertig
    [controller.brd, controller.sch]
2013-05-26 Jumper zum Board hinzugefügt
    [controller.brd, controller.sch]
2013-05-29 Layout-Tweaks, alle LEDs nun nebeneinander
    [controller.brd]
2013-06-05 Mehr Abstand in der GND-Isolation
    [controller.brd]
2013-06-06 * Platinenlayout nochmal angepasst (hauptsächlich Leiterbahndicken) * dritten Bus-Stecker vorgesehen
    [controller.brd, controller.sch]
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2013-06-15 initial hardware axis
    [Schluesselhalter.dwg, Schluesselhalter.stl]
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2013-08-02 added missing files
    [controller.brd]
2013-08-06 Schematics und Board für Manuellsteuerung
    [manuellsteuerung.brd, manuellsteuerung.sch]
2013-08-06 controller.brd hier nicht benötigt
    [controller.brd]
2013-08-08 Repository-Inhalt in eigenem Verzeichnis -> für Merge mit netz39_rollladensteuerung
    [schaltplan_v2.brd, schaltplan_v2.sch, swichboard.brd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]
2013-08-08 * README ins Hauptverzeichnis * swichboard -> switchboard
    [switchboard.brd, switchboard.sch]
2013-08-08 Kleine Anpassungen am Layout – Zahl der Drahtbrücken ist geblieben. :/
    [manuellsteuerung.brd]
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2013-09-03 Bug finally fixed :)
    [firmware.c]
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2013-10-04 Error check on I2C command and result transmission
    [firmware.c]
2013-10-04 Error checking methods on I2C command transmission
    [shuttercontrol.c]
2013-10-05 Correct switch assignments
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2013-10-24 Switch-Adressen korrigiert
2013-10-25 Correct use of functions; C lets you do any crap!
    [shuttercontrol.c]
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2013-11-23 Switch für den Watchdog
    [wd-switch.brd, wd-switch.sch]
2013-11-24 * Bohrlöcher xD * kleine Verbesserungen im Platinenlayout
    [wd-switch.brd, wd-switch.sch]
2013-11-24 Pinheaders für statische Schalterstellung
    [wd-switch.brd, wd-switch.sch]
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2013-12-01 Werte für die Kondensatoren angegeben
    [wd-switch.brd, wd-switch.sch]
2013-12-04 Fertige Schematics der Türsteuerung
    [tuer-steuerung.sch]
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2013-12-04 Erster Entwurf Board Türsteuerung
    [tuer-steuerung.brd]
2013-12-05 * Kleine Anpassungen in der Schaltung * Layout der Peripherie
    [tuer-steuerung.brd, tuer-steuerung.sch]
2013-12-06 Alex' Verbesserungen eingearbeitet und Layout fortgesetzt
    [tuer-steuerung.brd, tuer-steuerung.sch]
2013-12-07 Layout vollständig (nur 3 Drahtbrücken! \o/)
    [tuer-steuerung.brd, tuer-steuerung.sch]
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2013-12-10 Quartz-Positionierung gemäß Application Note
    [tuer-steuerung.brd]
2013-12-15 Tür-Controller (I2C-Gegenstelle zur Tür-Steuerung)
    [tuer-controller.brd, tuer-controller.sch]
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2013-12-16 Mindesgrößen der Pads und Vias angepasst
    [tuer-controller.brd, tuer-steuerung.brd]
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2013-12-19 Korrigiertes Design
    [wd-switch.brd, wd-switch.sch]
2013-12-21 WD-Switch jetzt mit Relais
    [wd-switch.brd, wd-switch.sch]
2013-12-22 kleine Layoutanpassung, um GND-Durchlass zu verbreitern
    [wd-switch.brd, wd-switch.sch]
2013-12-22 Korrigiertes M4-Relais eingesetzt
    [wd-switch.brd, wd-switch.sch]
2014-01-02 Integrierter I³C-Pegeladapter mit WatchDog-Switch
    [wd-adapter.brd, wd-adapter.sch]
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2014-01-05 Fehlendes Routing fehlt m(
    [wd-adapter.brd]
2014-01-12 Tür-Controller: Taster für Not-Auf und Space-Pause (gemäß Workshop zur Schließanlage)
    [tuer-controller.brd, tuer-controller.sch]
2014-01-15 Anschlussklemmen durch die richtigen Typen ersetzt und Mini-Tweaks
    [tuer-steuerung.brd, tuer-steuerung.sch]
2014-01-16 Letzte Anpassungen vor dem Ätzen
    [tuer-steuerung.brd, tuer-steuerung.sch]
2014-01-22 andere Holes, Beschriftung, eine Leiterbahn leicht verschoben
    [tuer-steuerung.brd]
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2014-01-29 Dokumentation Tür-Gehäuse von Hichi
    [00_Bill_of_materials.ods, 01_Hardware_00.stp, Endschalter-Haelfte2.dxf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]
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2014-01-31 i2cbridge: fix Makefile
2014-01-31 i2cbridge: fix sprintf path length
2014-01-31 i2cbridge: fix sun_family and addrsize
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2014-01-31 i2cbridge: fix i2c handling
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2014-01-31 i2cbridge: fix i2c poll bug
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2014-02-03 DXF für das Ausfräsen die Platine
    [tuer-controller-dim.dxf]
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2014-02-06 * LED-Richtung geprüft * Port-Config korrigiert m( * ein paar Tests
    [firmware.c]
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2014-02-09 doofen Fehler korrigiert
    diese Version läuft jetzt auch auf dem Schloss
    [firmware.c]
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2014-02-26 I³C adapter has been moved to https://github.com/netz39/i2cbridge
    [wd-adapter.brd, wd-adapter.sch, wd-switch.brd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]
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2014-07-12 Tür-Schalter: Aussparung an Top
    [skizze.fcstd]
2014-07-12 Shuttercontrol: Remove door control, as it is no longer needed.
    [shuttercontrol.c]
2014-08-18 Files in ein Unterverzeichnis verschoben
    [Motor.dwg, Schluesselhalter.dwg, Schluesselhalter.stl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]
2015-12-05 door-open: Error count and reset on I2C problems
    Count I3C transmission errors and reset the system if there are too many
    errors in a row.
    Also logs actions to the shuttercontrol log.
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2016-04-30 Debounce demo code quality
    Add fixes regarding https://github.com/netz39/rollladensteuerung/pull/1#issuecomment-214857090
    [firmware.c]
2016-07-10 Debounce: Correct pattern for button down and up
    Set the correct patterns for debounce_is_button_down and debounce_is_button_up.
    (The values were mixed up.)
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2018-12-30 PiHat: first draft revision
    [pi-hat.kicad_pcb, pi-hat.sch]
2019-01-06 PiHat: 2nd revision
    * Checked and adapted MOSFET high-side switches
    * remove J6 for space and fix mounting hole
    * Fix Molex connectors
    * Capacitors
    * Extension board positions
    * General layout
    [pi-hat.kicad_pcb, pi-hat.sch]
2019-01-06 Final fixes
    * make sheet bigger (A3) to fix everything nicely
    * fix INT LED to be low active
    * fix molex holes
    * fix base resistors
    [pi-hat.kicad_pcb, pi-hat.sch]
2019-01-07 Add matching resistors to I3C lines
    [pi-hat.kicad_pcb, pi-hat.sch]
2019-01-07 Ground management and max rating for output
    [pi-hat.kicad_pcb]
2019-01-19 Remove some level shifters
    The level shifters made only sense for I3C - removed the rest.
    [pi-hat.kicad_pcb, pi-hat.sch]
2019-01-27 Run RenumKicadPCB to sort designators
    https://github.com/penguineer/RenumKicadPCB
    [pi-hat.kicad_pcb, pi-hat.sch]
2019-01-27 Final pass for board fillings
    [pi-hat.kicad_pcb]
2019-07-20 Wait 0.5s if I2C failed
    [door-service.py]
2019-07-20 Fix: Zero return from I3C is error condition
    [door-service.py]
2019-07-21 Don't log SMBus errors
    Those errors can be treated and only fill up the log.
    [door-service.py]
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

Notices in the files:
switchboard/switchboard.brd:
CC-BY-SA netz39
